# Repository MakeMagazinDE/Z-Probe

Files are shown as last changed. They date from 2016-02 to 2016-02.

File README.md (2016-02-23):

GitHub Logo

Maker Media GmbH und c't, Heise Zeitschriften Verlag

***

# Z-Probe
Z-Längentaster für CNC-Maschinen, kapazitiv

Die Schaltung kann mit +5V oder +12V bis +24V versorgt werden. Bei 5-V-Versorgung ist JP3 zu überbrücken. Höhere Betriebsspannungen als 24V sind möglich, wenn man R7..R9 durch den Wert 2k2 ersetzt.

Die Empfindlichkeit wird von C1 bestimmt - kleinere Werte ergeben höhere Empfindlichkeit. LED1 leuchtet bei Berührung der Schaltfläche auf (Berührung zum Test mit dem Finger). Sobald die (parasitäre) Kapazität an der Schaltfläche größer wird als C1, spricht die Schaltung an. Bei durchgehender Massefläche auf der Rückseite (doppelseitige Platine) ist die Kapazität der Elektrode nach Masse von sich aus schon recht hoch. C1 sollte dann mit 22p bemessen werden. 

Üblicherweise sollte JP1 für eine negative Logik (Ausgang schaltet bei Berührung nach Masse) überbrückt sein. Sollte die CNC-Steuerung eine positive Logik (Ausgang normal auf Masse, bei Berührung offen bzw. "high") verlangen, ist stattdessen JP2 zu überbrücken.

Layout für doppelseitige Platine als Gerber- und PDF-Dateien. Informationen für Selbstätzer: Rückseite vollständig Kupfer als Massefläche, zwei Durchkontaktierungen aus Kupferdraht nötig. Ggf. zwei Bohrungen für Steckverbinder auf Rückseite freikratzen.

Z-Probe-Eingang bei der aktuellen Version der GRBL-JOG-Firmware ist Pin 5 (PB4, SPI SS) des ATmega644. Dieser Eingang ist an PL7 (ISP) Pin 3 zugänglich. Für erhöhte Störsicherheit sollte ein Pull-up-Widerstand 4k7 nach +5V und ggf. ein Eingangsfilter wie an den anderen Schalter-Eingängen vorgesehen werden. Eine überarbeitete GRBL-JOG-Platine ist in Planung.

Bitte beachten Sie den Artikel in Make: 1/2016.

Carsten Meyer, Redaktion Make:

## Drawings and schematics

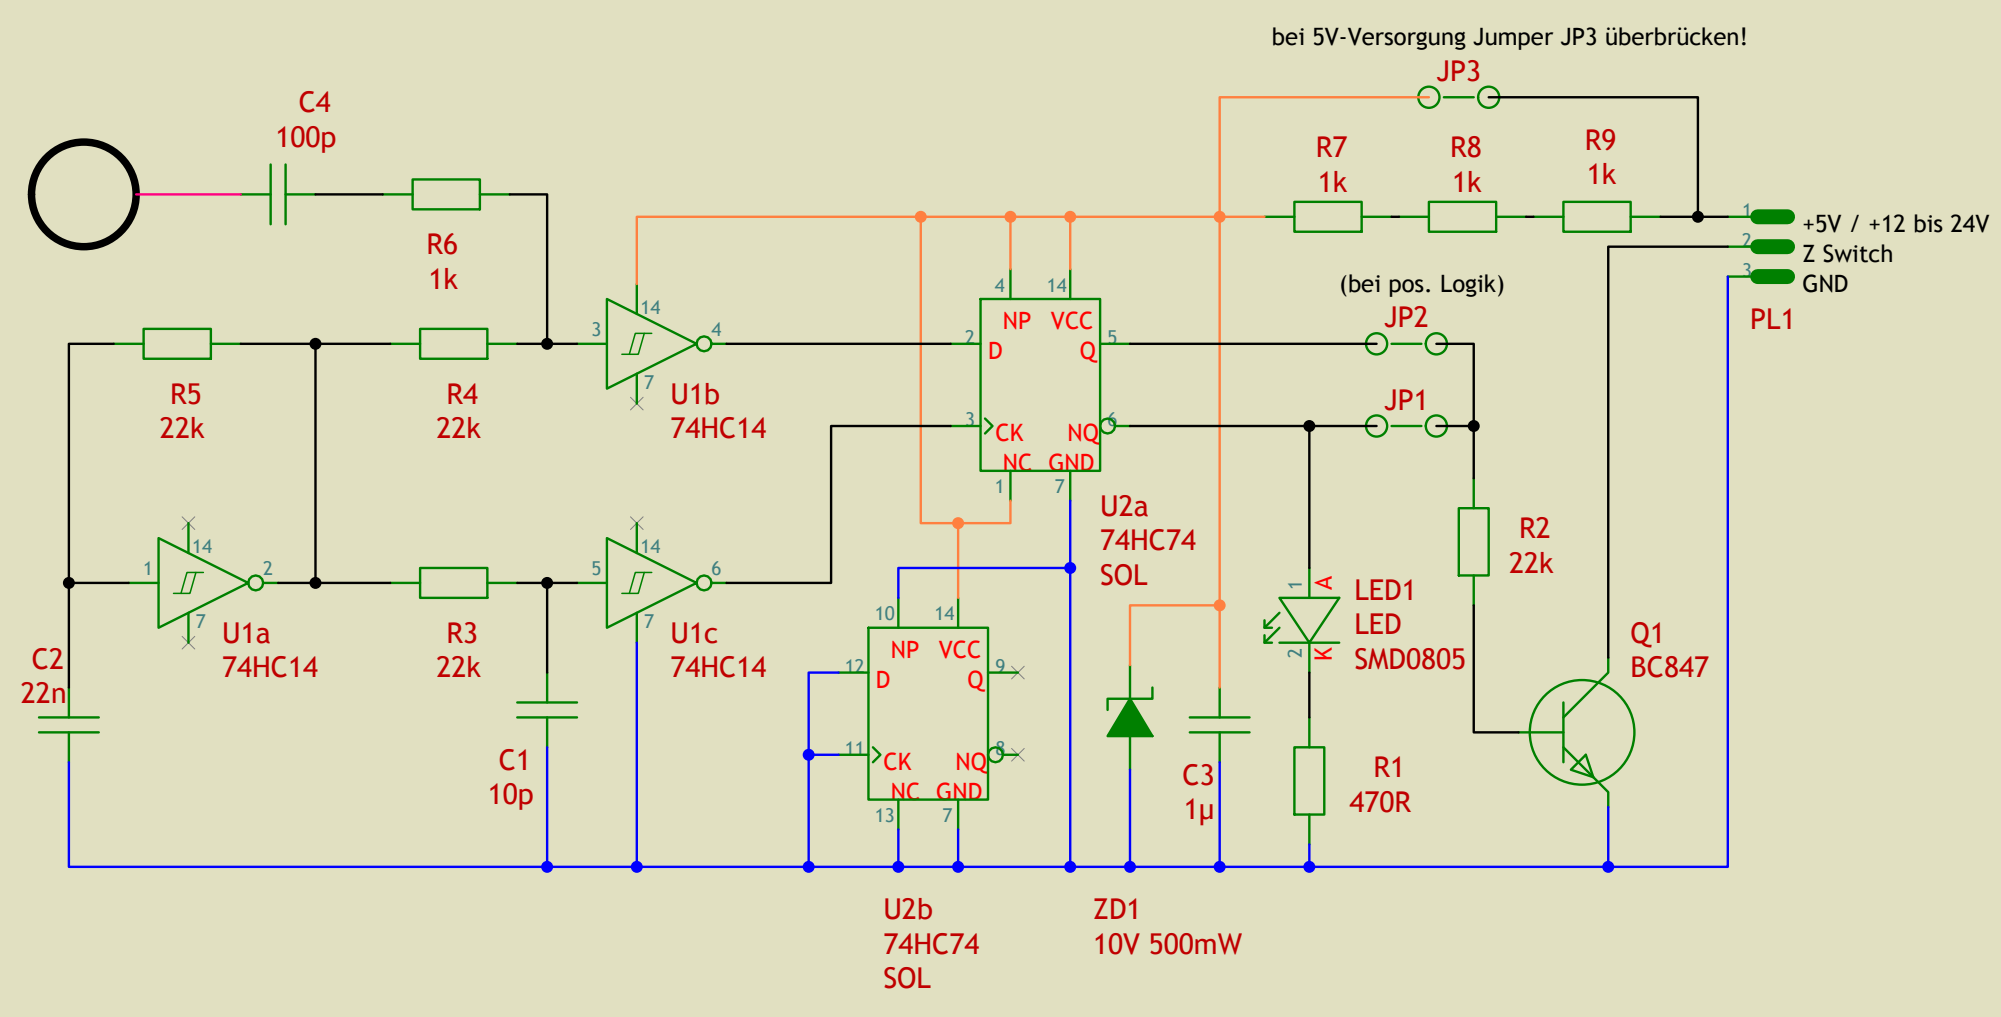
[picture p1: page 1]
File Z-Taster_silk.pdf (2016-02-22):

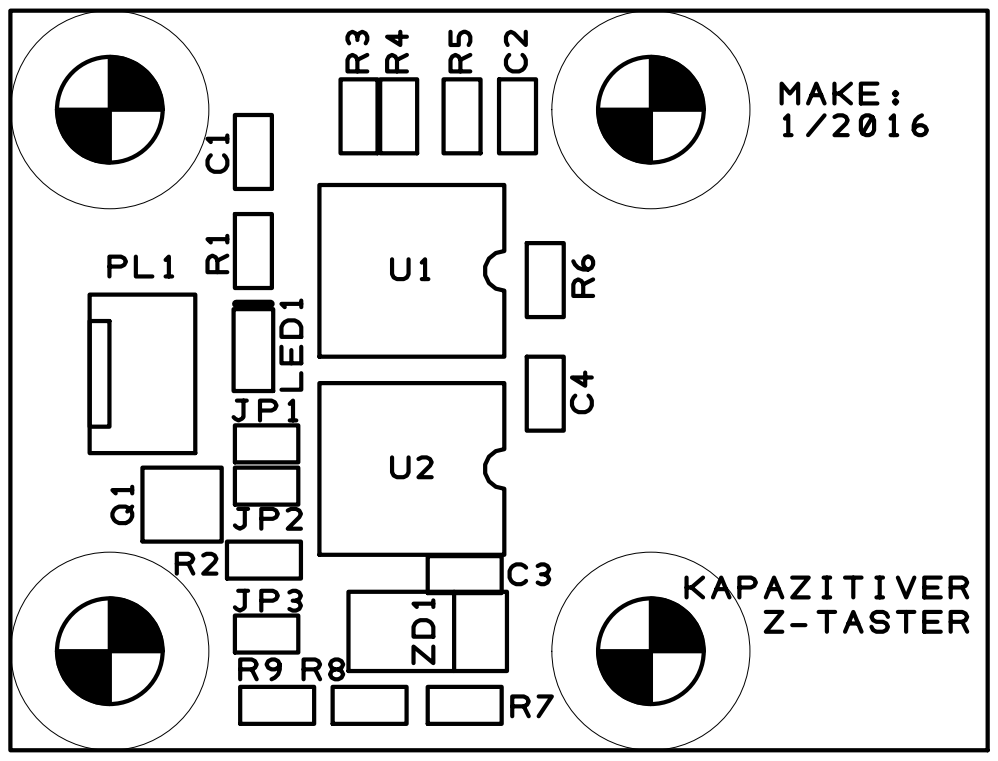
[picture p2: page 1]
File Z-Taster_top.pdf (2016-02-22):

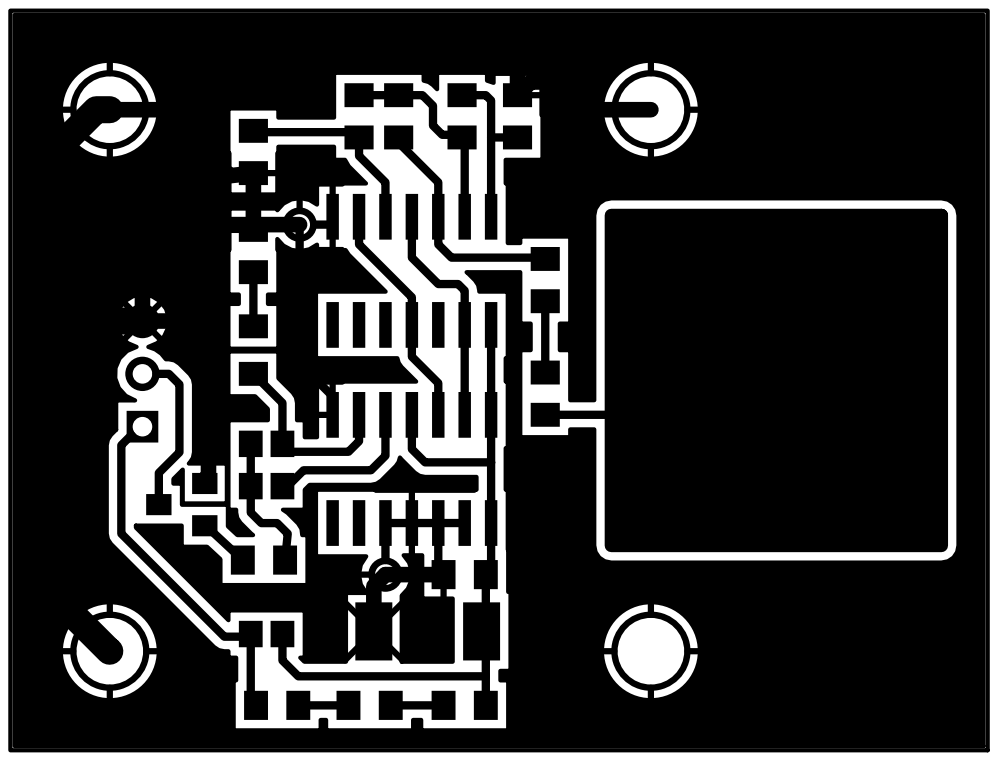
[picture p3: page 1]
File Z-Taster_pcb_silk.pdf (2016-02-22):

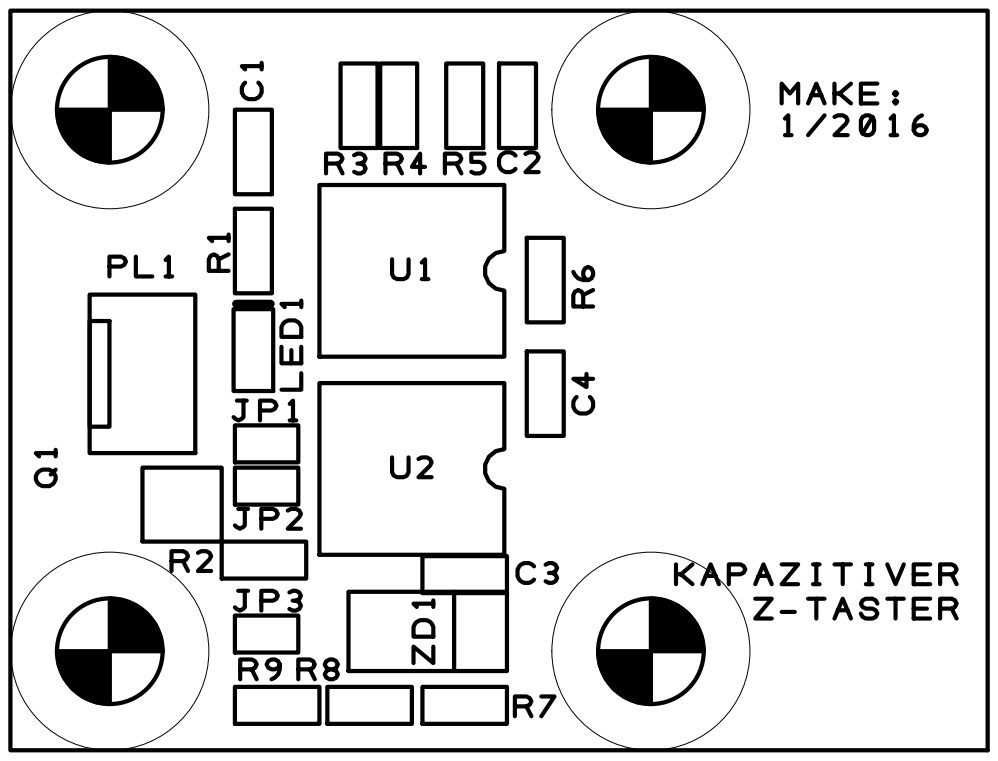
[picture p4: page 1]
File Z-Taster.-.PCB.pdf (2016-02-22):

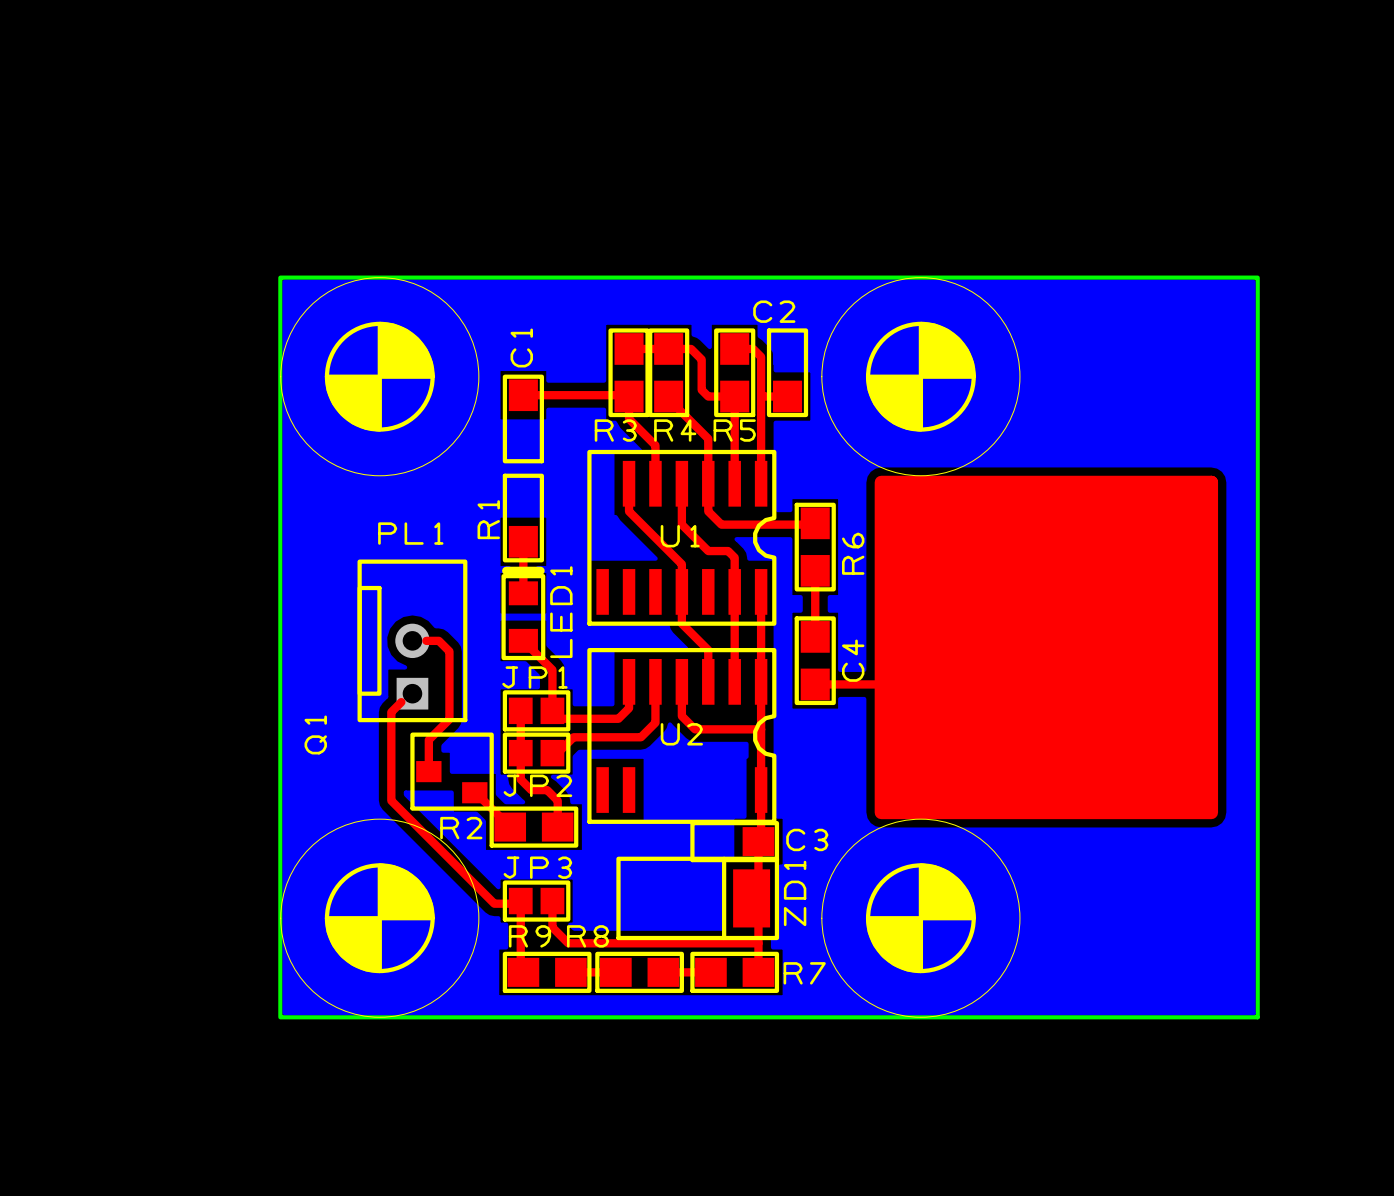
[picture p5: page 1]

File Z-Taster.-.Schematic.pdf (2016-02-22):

# bei 5V-Versorgung Jumper JP3 überbrücken!

# +5V / +12 bis 24V
